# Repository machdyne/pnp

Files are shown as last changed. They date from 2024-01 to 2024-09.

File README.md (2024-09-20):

# Machdyne PNP

## Overview

Machdyne PNP is an open-source project to describe and document the pick-and-place machines that we're using to assist with the assembly of some of our [products](https://machdyne.com).

Instead of a turnkey solution this project will aim to provide examples for anyone who wants (1) to build a custom pick-and-place machine in order to meet their own specific requirements, (2) to understand the machine from the top to bottom, and (3) to have the ability to maintain, modify and repair it.

These machines are designed to work with the [OpenPnP](https://github.com/openpnp/openpnp) software. Instead of attempting to recreate the OpenPnP documentation we will provide links and notes to help you move through the setup process. Our documentation will aim to fill the gaps that we encountered while researching how to build and use such a machine.

### [Machine Eins](machines/eins)

The machine consists of an extruded aluminum frame, linear guide rails, stepper motors, a vacuum pump, a solenoid valve, a controller board, two cameras and a number of 3D-printed parts. The non-printed parts are commonly available. The 3D parts are designed using OpenSCAD. Each part can be printed in about 3 hours or less which allows them to be quickly modified and replaced.

The machine is large (> 1m x 0.6m) but the design is scalable and can be used with a smaller (or larger) frame. The machine is relatively light-weight and must be securely mounted to a sturdy table. It requires a hole in the table for the up-facing camera.

The overall design was inspired by existing open-source pick-and-place machines, primarily the [IndexPnP](https://www.youtube.com/watch?v=YynPThPrJ0o) (the precursor to the [LumenPnP](https://github.com/opulo-inc/lumenpnp)) and [LitePlacer](https://github.com/openpnp/openpnp/wiki/LitePlacer), however all 3D parts have been designed from scratch.

### Machine Zwei

This is a future design based on our experience building and using Eins. Zwei will be more of an assembly assistant than a complete PnP machine. It will be more compact, somewhat portable and it won't require a dedicated table. It is intended for the production of boards with a small number of unique parts, or for placing the most common parts on a larger board (such as decoupling capacitors), or for precisely placing large components.

### [Machdyne AF](https://github.com/machdyne/af)

The [Machdyne AF](https://github.com/machdyne/af) project is a work-in-progress autofeeder system for our PNP machines.

## Funding

This project is being partially funded through the NGI0 Entrust Fund, a fund established by NLnet with financial support from the European Commission's Next Generation Internet programme.

## License

This project is released under the [CERN-OHL-P](LICENSE.txt) license.

The firmware configuration files are released under the GPL3 license.

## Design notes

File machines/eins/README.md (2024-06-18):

# Machdyne PNP - Eins

## Overview

Eins is a simple modular open-source pick and place machine. It is a work-in-progress and this repo will be kept up-to-date as improvements are made. Please feel free to open issues with questions or suggestions.

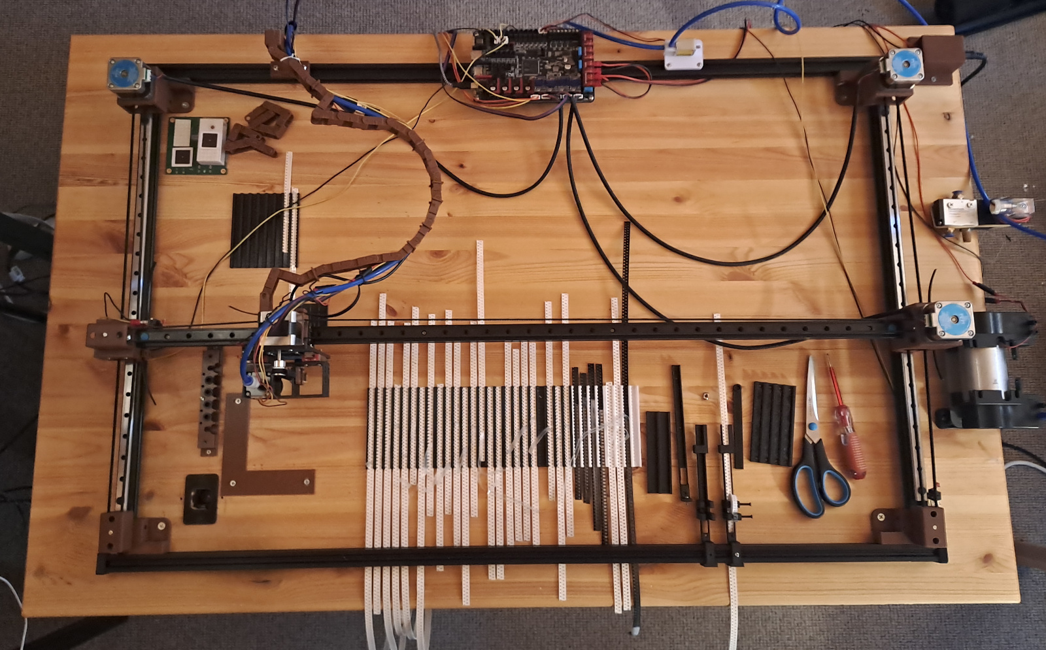
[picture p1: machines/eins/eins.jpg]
eins


This photo is from Jan 2024. You may notice an unused backup solenoid valve on the right side and some passive auto feeder prototypes. The tool changer and multi-strip feeders are not part of this project but can be found below:

  * [Tool changer](https://github.com/richardklingler/openpnp/tree/master/openscad/toolchanger)
  * [Strip feeder](https://www.thingiverse.com/thing:5711658)

The two Y axis motors are connected to a single driver, this is a feature of the controller board.

There is a [video](https://twitter.com/machdyne/status/1705911534369574982) of the machine in action.

## Specifications

| Attribute | Value |
| --- | ----- |
| Table size | 1200mm x 750mm |
| Machine size | ~1000mm x ~650mm |
| Work area | ~850mm x ~450mm |
| Minimum tested part size | 0402 |
| Max placement speed | YTBD |

## Documentation

  * [Assembly Guide](docs/ASSEMBLY.md)

## Parts

The 3D-printable parts are located in the [3d](3d) directory as [OpenSCAD](https://openscad.org) files. You can use OpenSCAD to customize and generate the [STL](3d/stl) files, which can then be sliced and printed.

| Part | Model | Quantity | Description |
| ---- | ----- | --- | --- |
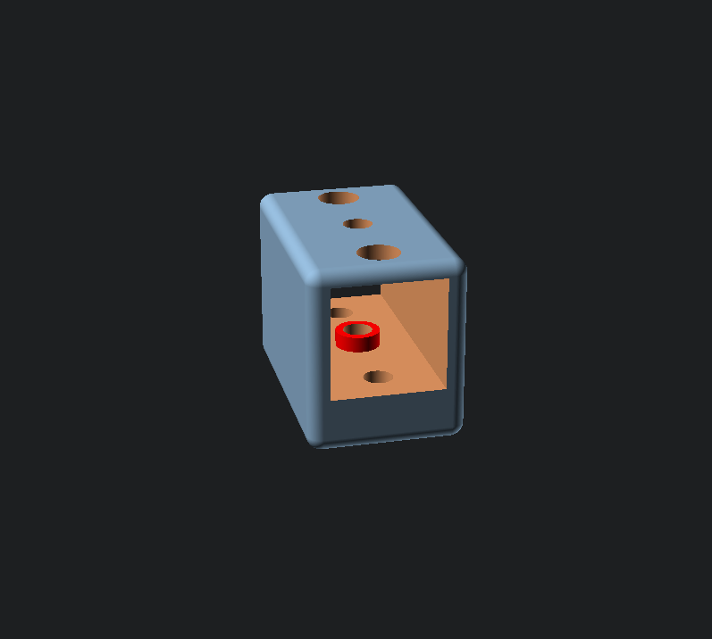
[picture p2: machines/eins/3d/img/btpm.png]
btpm
| [btpm](3d/stl/btpm.stl) |  | 3 | **Belt tension pulley mount.** Holds the belt in place at the opposite end of the axis as the motor, using a pulley and steel dowel. |
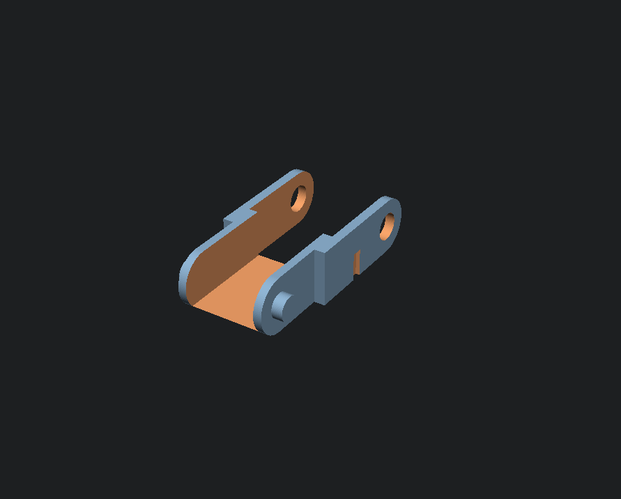
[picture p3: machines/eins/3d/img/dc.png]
dc
| [dc](3d/stl/dc.stl) |  | 1 | **Drag chain links, clips and tower.** Keeps wires, cables and tubing lifted above the work area. The current design sags a bit when the chain is long and needs to be improved. We recommend using a commodity dragchain instead. |
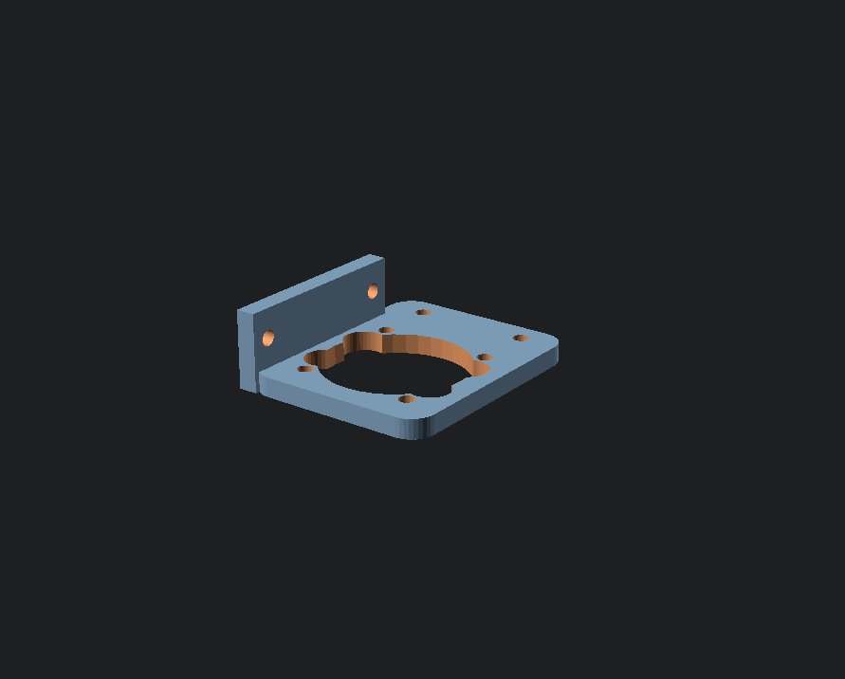
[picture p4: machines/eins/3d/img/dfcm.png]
dfcm
| [dfcm](3d/stl/dfcm.stl) |  | 4 | **Down-facing camera mount.** Holds the down-facing camera. Attaches to the bottom rear side of the Z Gantry Mount Faceplate. |
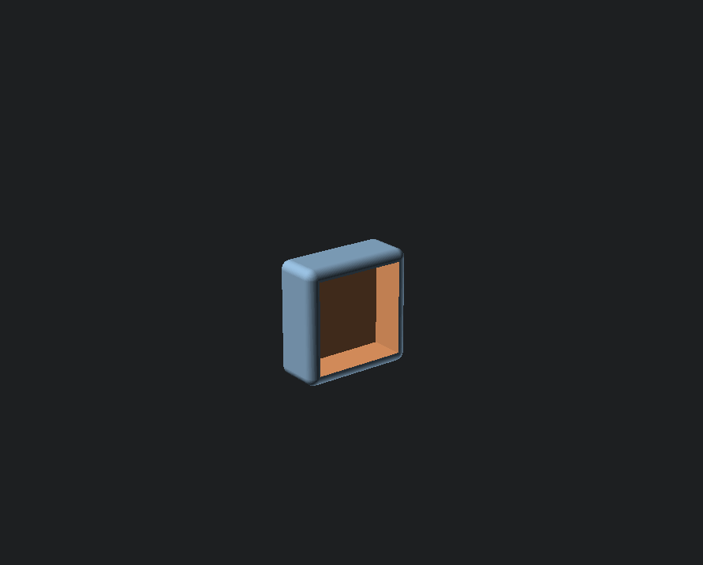
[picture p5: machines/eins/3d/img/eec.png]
eec
| [eec](3d/stl/eec.stl) |  | 1 | **Extrusion end cap.** Covers sharp edges at the ends of the aluminum extrusions. |
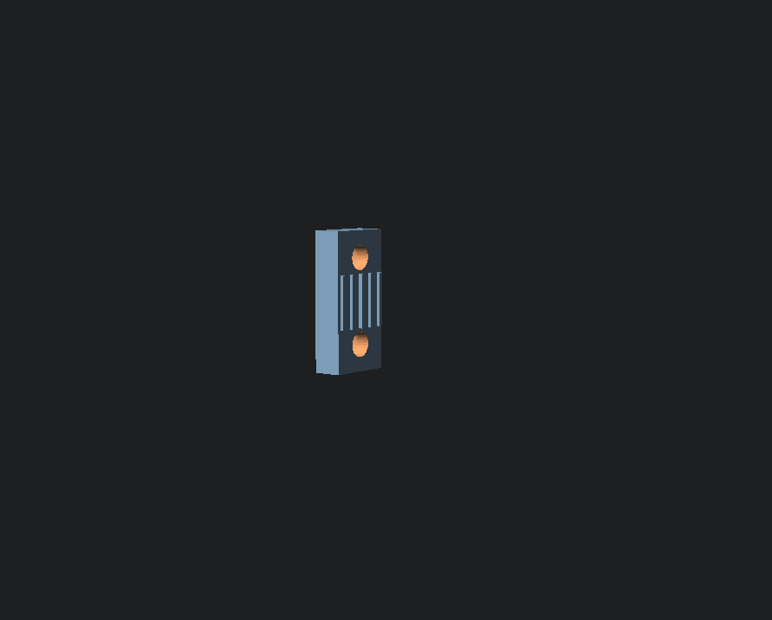
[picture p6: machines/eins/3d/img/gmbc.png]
gmbc
| [gmbc](3d/stl/gmbc.stl) |  | 6 | **Gantry mount belt clamp.** Attaches belt ends to gantry mounts. |
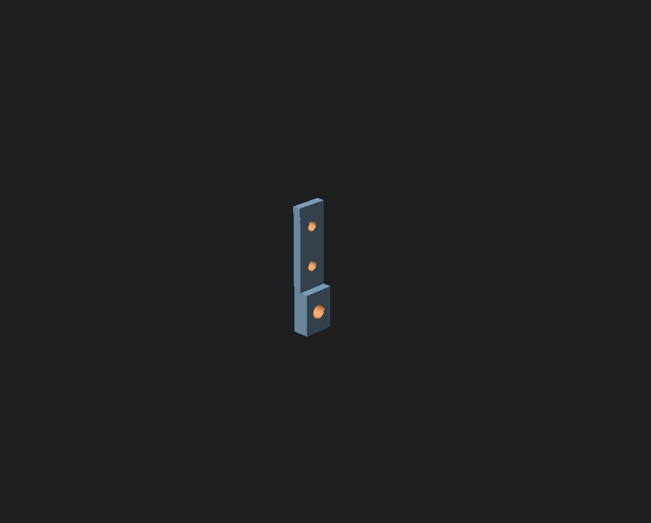
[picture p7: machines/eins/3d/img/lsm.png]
lsm
| [lsm](3d/stl/lsm.stl) |  | 2 | **Limit switch mount.** Attaches X and Y limit switches to the frame. |
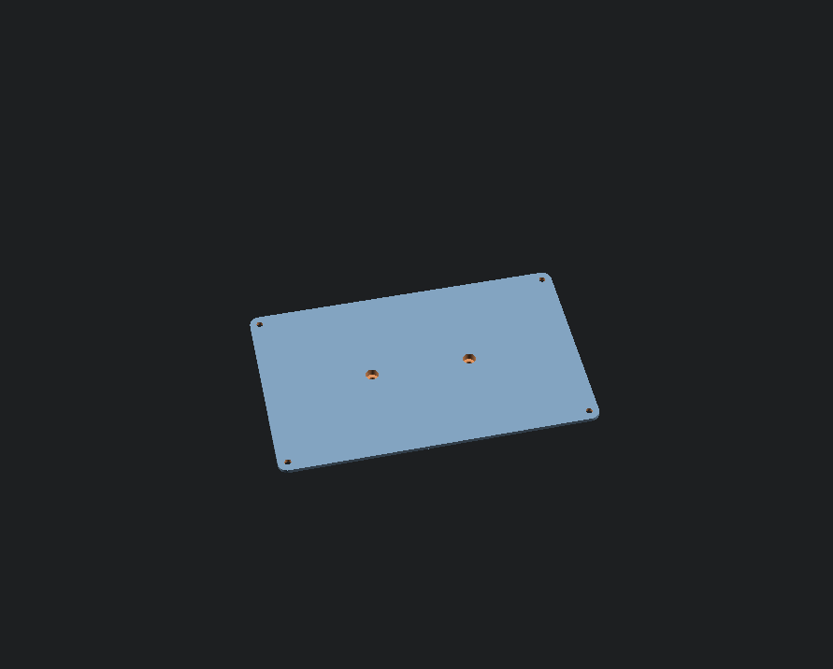
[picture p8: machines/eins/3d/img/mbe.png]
mbe
| [mbe](3d/stl/mbe.stl) |  | 1 | **Mainboard enclosure.** Mounts the controller board to the frame. Not actually enclosed at the moment. |
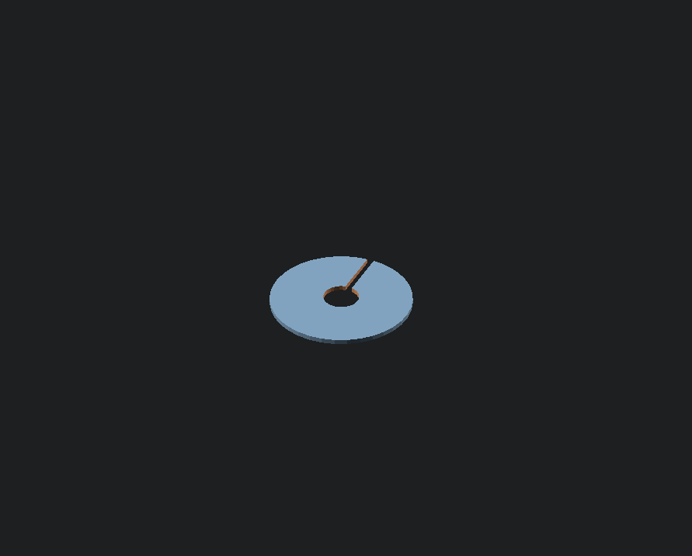
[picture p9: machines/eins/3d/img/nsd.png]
nsd
| [nsd](3d/stl/nsd.stl) |  | 1 | **Nozzle shade disc.** Reduces reflections from the up-facing camera lights on motor. |
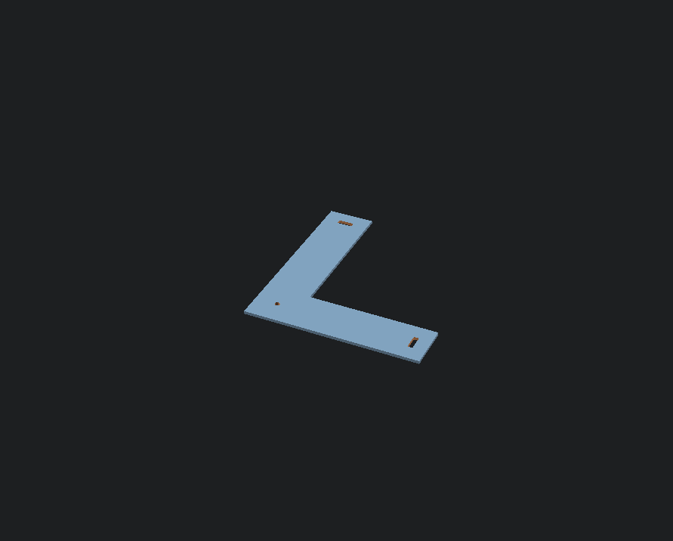
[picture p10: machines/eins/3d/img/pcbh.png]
pcbh
| [pcbh](3d/stl/pcbh.stl) |  | 1 | **PCB holder.** Holds the PCB during assembly. Top screw also acts as homing position. |
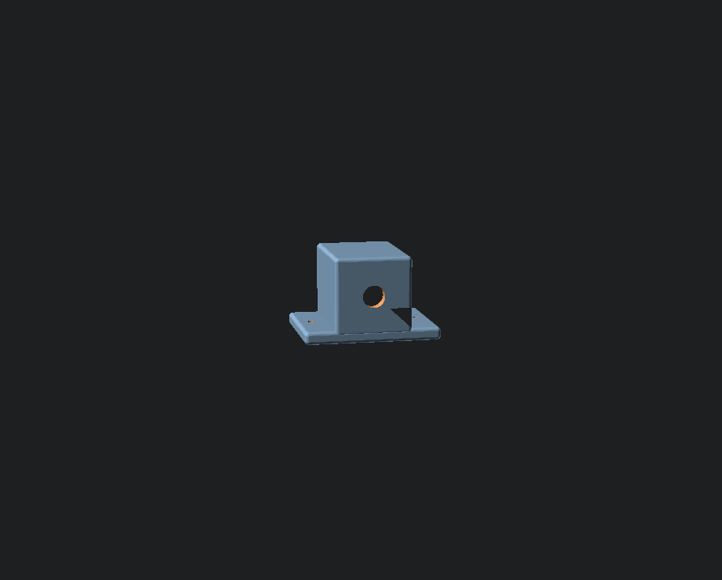
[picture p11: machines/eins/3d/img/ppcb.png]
ppcb
| [ppcb](3d/stl/ppcb.stl) |  | 1 | **Power plug connection box.** Adapts the power supply plug to the controller board. |
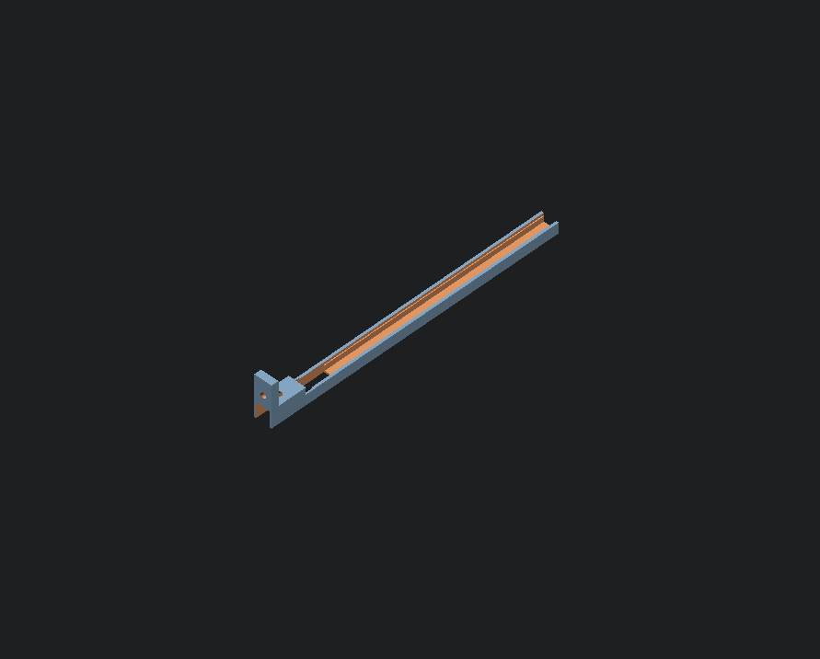
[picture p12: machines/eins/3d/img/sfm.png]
| [sfm](3d/stl/sfm.stl) |  | 1 | **Strip feeder manual.** Manual single feeder for 8mm tapes. |
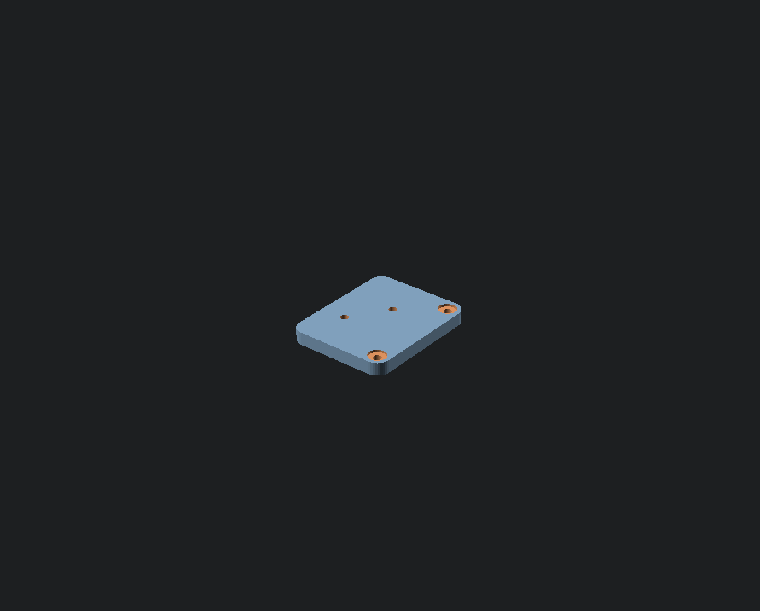
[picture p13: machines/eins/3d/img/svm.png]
| [svm](3d/stl/svm.stl) |  | 1 | **Solenoid valve mount.** Mounts the solenoid valve to the frame. |
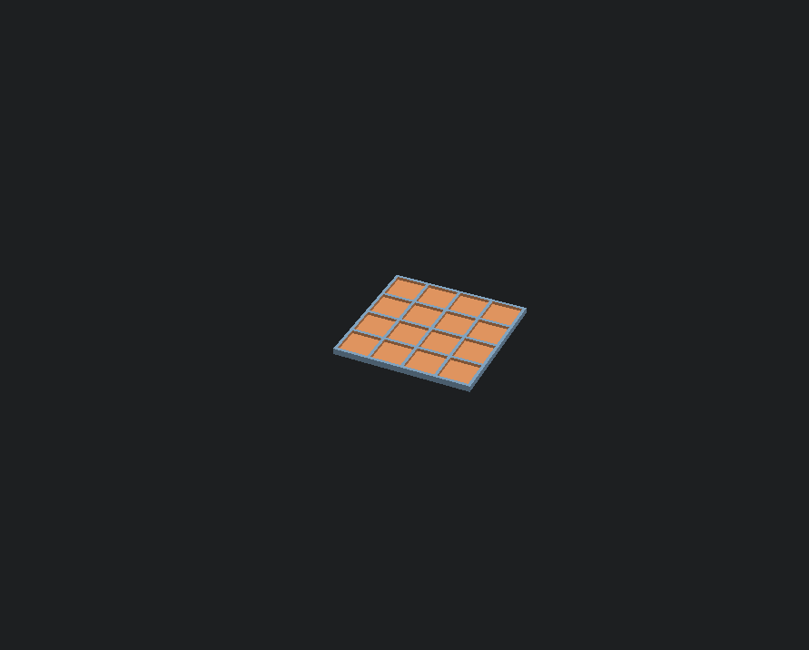
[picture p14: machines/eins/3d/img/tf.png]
tf
| [tf](3d/stl/tf.stl) |  | 1 | **Tray feeder.** Generic customizable tray feeder for ICs. Can be attached to the table with tape. |
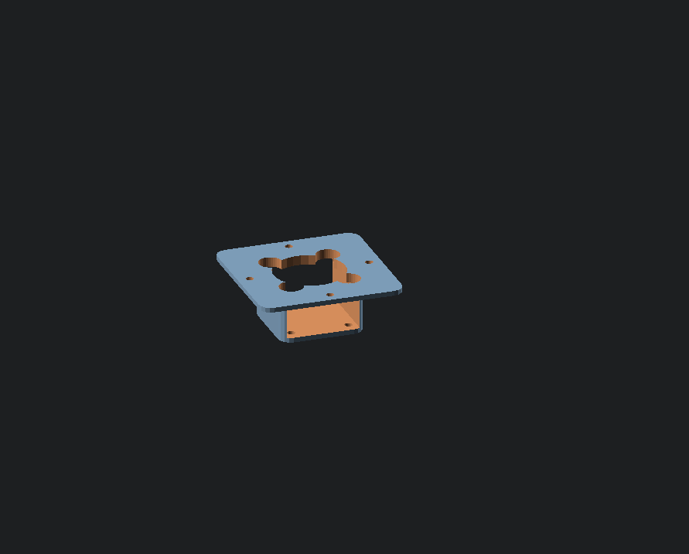
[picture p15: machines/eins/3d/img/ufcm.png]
ufcm
| [ufcm](3d/stl/ufcm.stl) |  | 1 | **Up-facing camera mount.** Mounts the bottom camera underneath the table. |
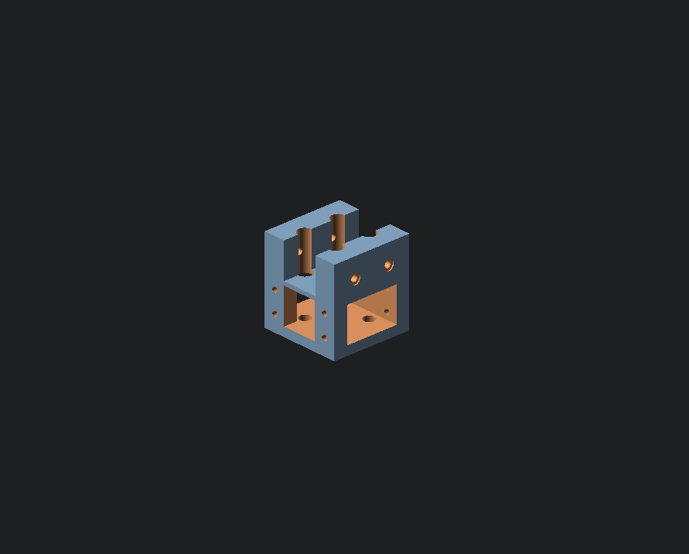
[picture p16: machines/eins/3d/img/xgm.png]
xgm
| [xgm](3d/stl/xgm.stl) |  | 2 | **X gantry mount.** Mounts the X gantry to the Y axis rail. |
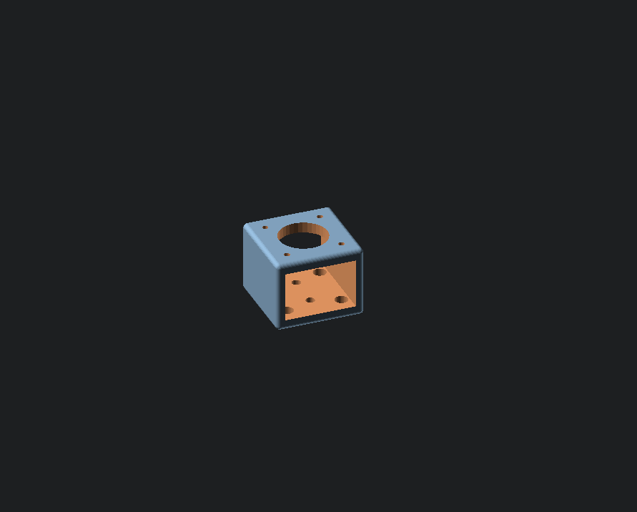
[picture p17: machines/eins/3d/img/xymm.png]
xymm
| [xymm](3d/stl/xymm.stl) |  | 3 | **X+Y motor mount.** Mounts the X and Y motors to their axes. |
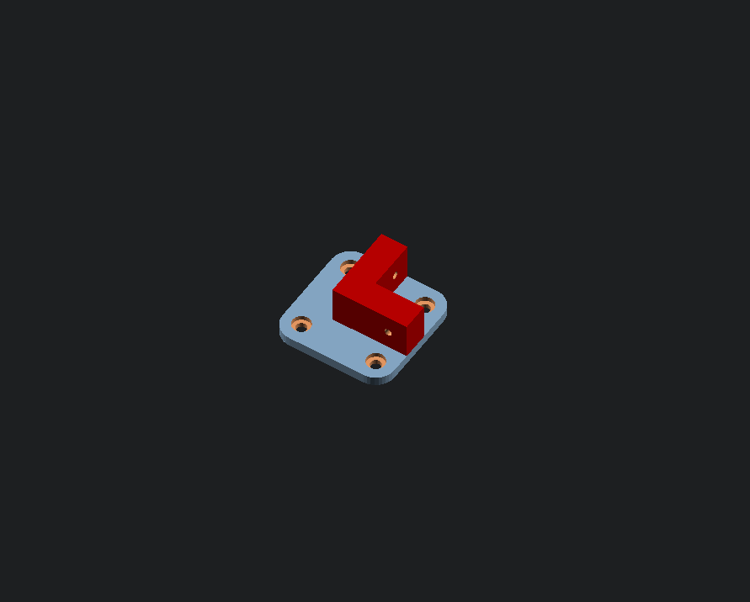
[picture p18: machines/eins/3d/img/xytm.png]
xytm
| [xytm](3d/stl/xytm.stl) |  | 4 | **X+Y table mount.** Mounts the machine to the table. |
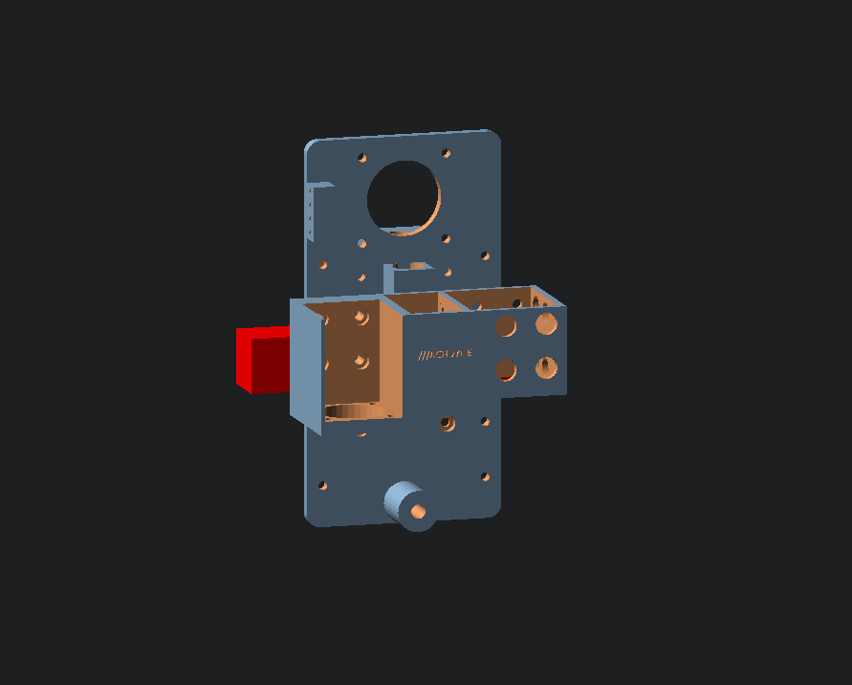
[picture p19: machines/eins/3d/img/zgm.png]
zgm
| [zgm](3d/stl/zgm.stl) |  | 1 | **Z gantry mount, faceplate and assembly mount.** The Z gantry mount ([zgm](3d/stl/zgm.stl)) connects to the belt ends and sits on the X axis. Attached to the zgm is the Z gantry mount faceplate ([zgmfp](3d/stl/zgmfp.stl)) where the Z axis rails are mounted, and to those rails, the Z assembly mount ([zam](3d/stl/zam.stl)), which moves along the Z axis. The Z limit switch attaches to the upper left of the faceplate. |

## Bill of Materials

| Part | Quantity | Description | Example P/N |
| ---- | --- |--- | --- |
| Controller board | 1 | BIGTREETECH Octopus V1.1 Controller board + 4x TMC2209 drivers | KINPRINT-UUU001949 |
| (a) Stepper motors | 4 | 42x42x38mm, 1.68A, 1.8deg, 1.65ohm | 800-001-0782 |
| or (b) Stepper motors | 4 | 42x42x38mm, 1.5A, 0.9deg, 2ohm | 17ME15-1504S |
| Hollow stepper motor set | 1 | 28mm NEMA 11 hollow shaft, D6 rotary joint, CP40 holder | |
| Nozzles | 1+ | CP40 nozzles, N045, N14, N24 | |
| Power supply | 1 | Enclosed desktop supply, 24V 5A 120W, 2.5mm plug | GST120A24-P1M |
| Power jack | 1 | 2.5mm power socket | DC-099 |
| Cameras | 2 | 1MP USB modules | HBV-W202012HD |
| LEDs | 12 | White LEDs 5mm | |
| Vacuum pump | 1 | 24V 10-15L/min 6mm ID | B0BVZR96HN |
| Solenoid valve | 1 | 24V N/O 4mm ID | | 
| Pneumatic tubing | 1 | 6mm ID + 4mm ID + adapters + couplers | | 
| Limit switches | 3 | Roller lever 3 pin limit switches | B07F9QKTQQ |
| Frame X axes | 3 | Aluminum extrusion, 2020V, 1000mm | AW051-2020V-1000 |
| Frame Y axes | 2 | Aluminum extrusion, 2020V, 600mm | AW051-2020V-600 |
| Rail X axis | 1 | Linear rail, MGN12H, 900mm | MGN12H1R900-1 |
| Rail Y axes | 2 | Linear rails, MGN12H, 500mm | 4801151PQ8 |
| Rail Z axes | 2 | Linear rails, MGN9H, 100mm | B08GWVV75C |
| Steel dowels | 3 | 5mm diameter x 25mm long | B07NXPQ717 |
| GT2 belt kits | 2 | Belts and pulleys, 6mm wide, 2mm pitch | B07RBK4GRL |
| Drag chain | 1 | 10x20 drag chain; 1m | 734900622184 |

Note: Use the (a) stepper motors if more concerned with speed; or the (b) stepper motors if more concerned with accuracy.

You will need an assortment of lengths of M3 and M5 bolts, nuts and T-nuts and screws. You will also need some M2 bolts and nuts to attach the limit switches.

## Tools

In addition to a 3D printer you will likely need a variety of tools, including screwdrivers, wire strippers, crimpers, a soldering iron, a drill, etc.

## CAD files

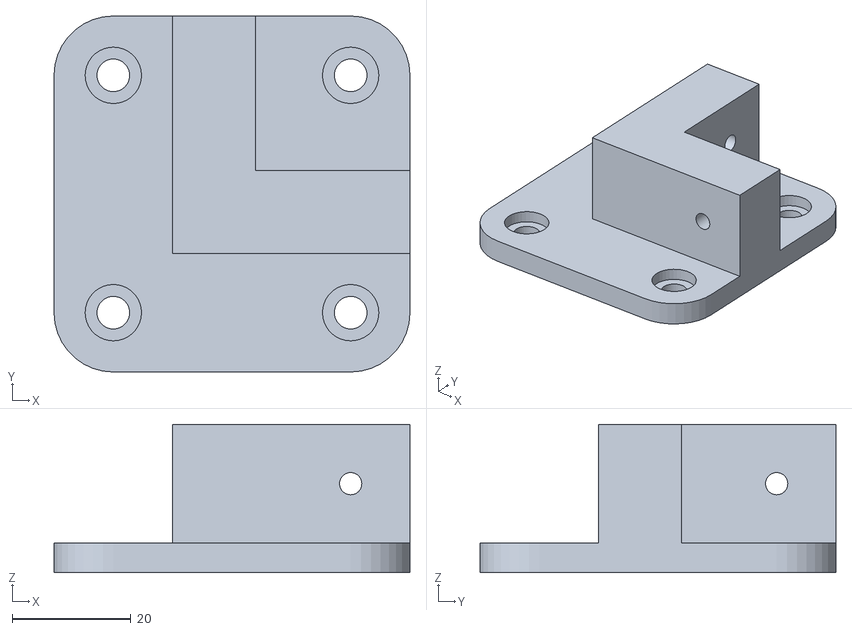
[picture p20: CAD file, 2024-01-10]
machines/eins/3d/stl/xytm.stl
60.0 x 60.0 x 25.0

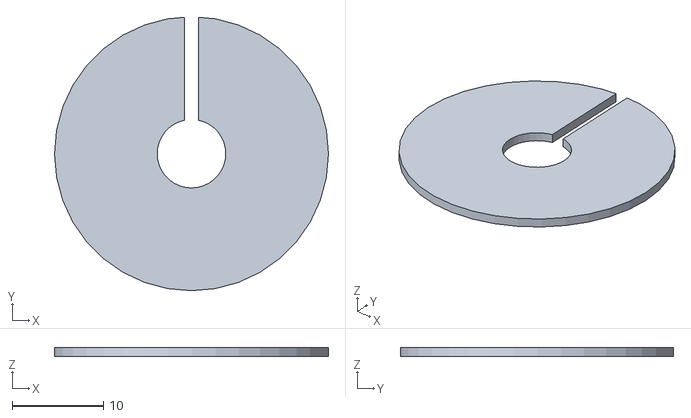
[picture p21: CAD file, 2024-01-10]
machines/eins/3d/stl/nsd.stl
30.0 x 29.9 x 1.00

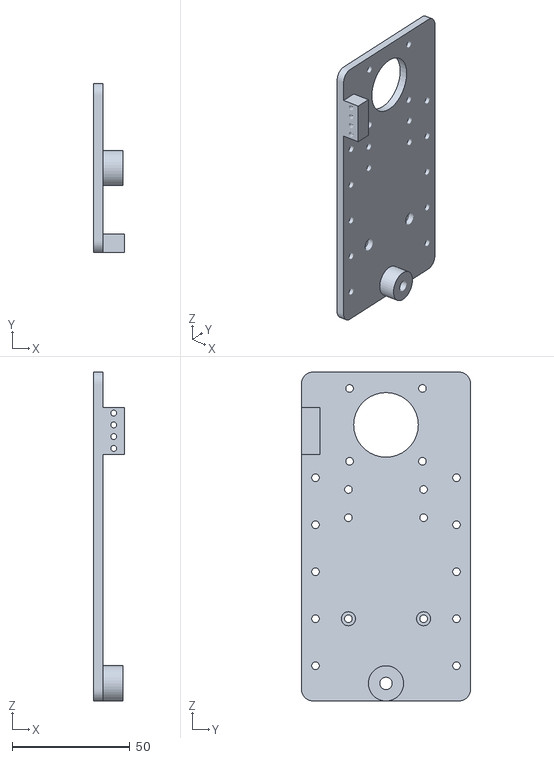
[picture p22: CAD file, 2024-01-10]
machines/eins/3d/stl/zgmfp.stl
13.0 x 72.0 x 140.0

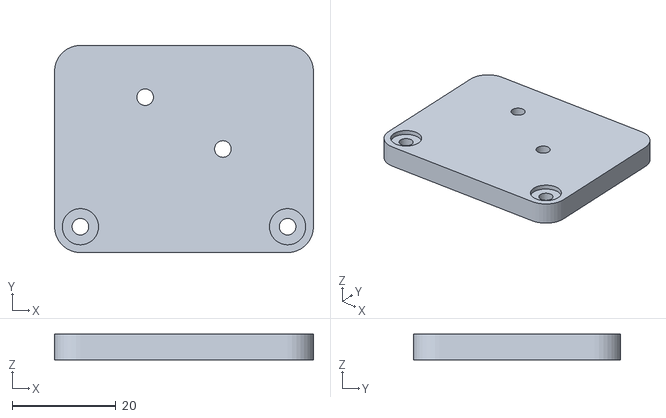
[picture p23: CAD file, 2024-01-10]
machines/eins/3d/stl/svm.stl
50.0 x 40.0 x 5.00

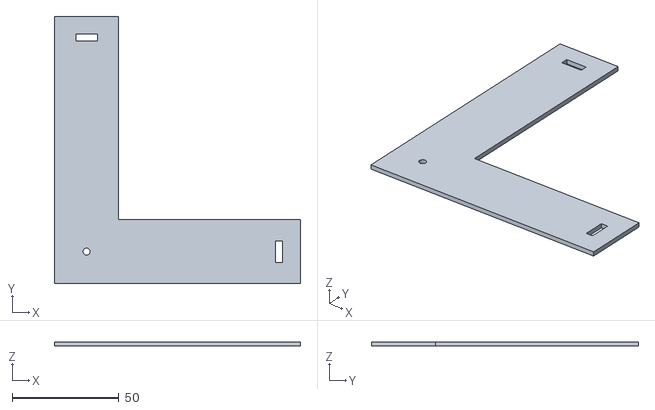
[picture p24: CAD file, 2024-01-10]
machines/eins/3d/stl/pcbh.stl
115.0 x 125.0 x 2.00

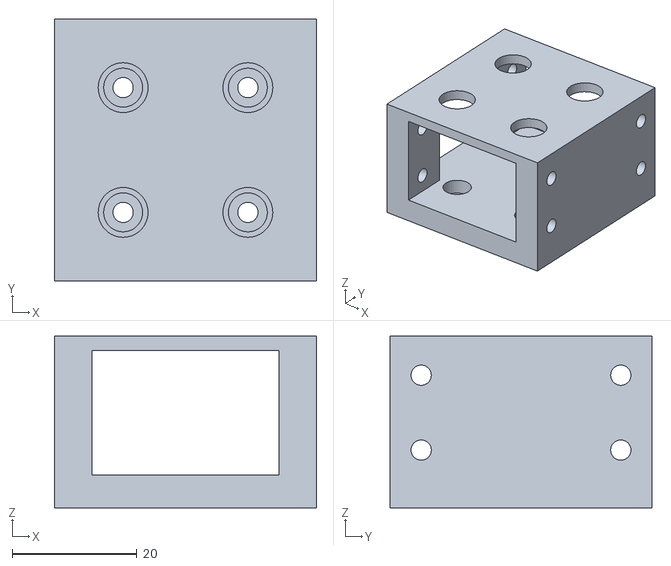
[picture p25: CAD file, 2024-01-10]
machines/eins/3d/stl/zgm.stl
42.0 x 42.0 x 27.5

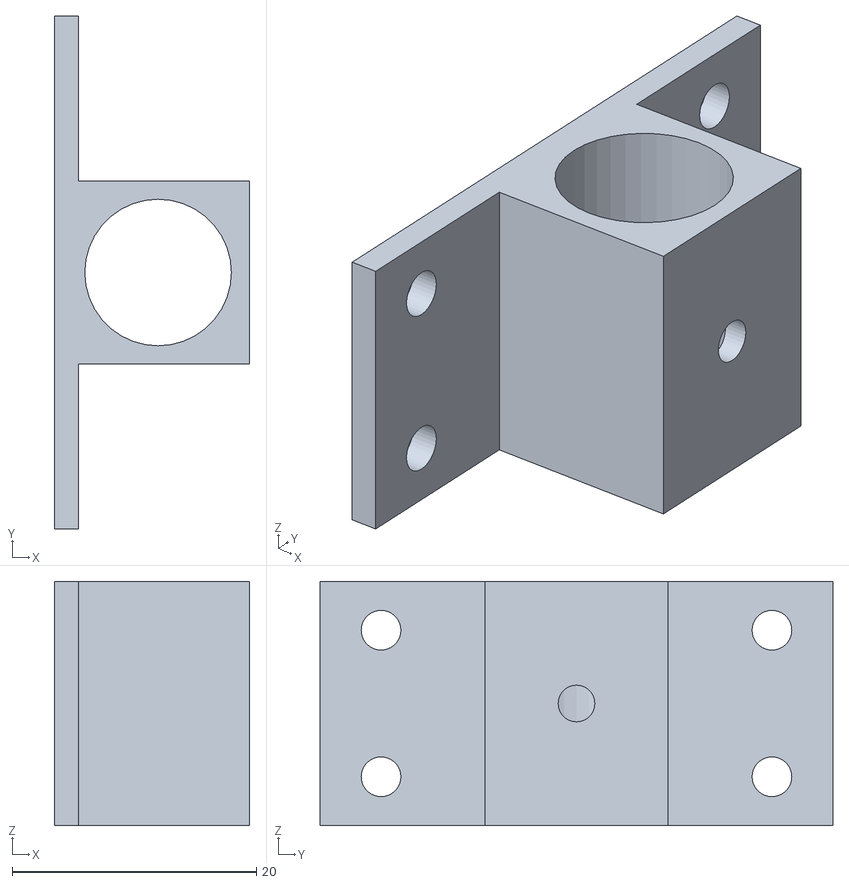
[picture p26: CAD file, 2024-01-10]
machines/eins/3d/stl/zgmfpp.stl
16.0 x 42.0 x 20.0

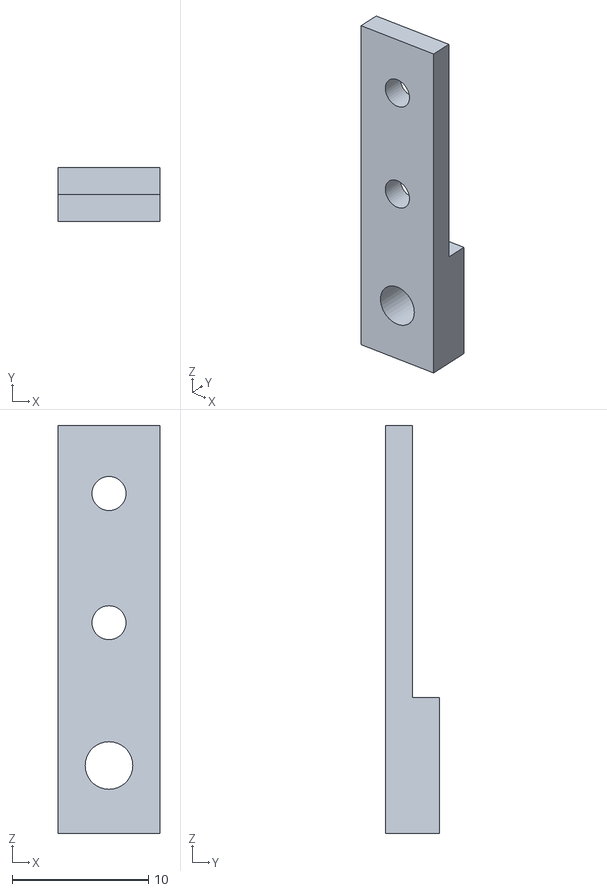
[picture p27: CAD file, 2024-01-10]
machines/eins/3d/stl/lsm.stl
7.50 x 4.00 x 30.0

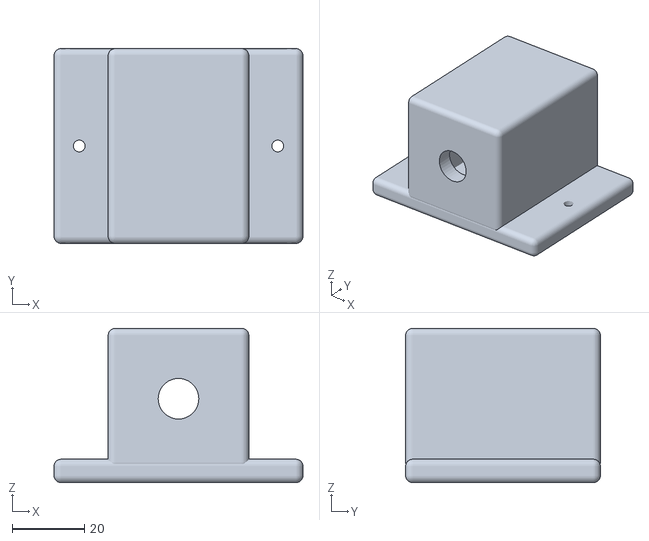
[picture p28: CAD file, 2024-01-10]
machines/eins/3d/stl/ppcb.stl
69.0 x 54.0 x 42.7

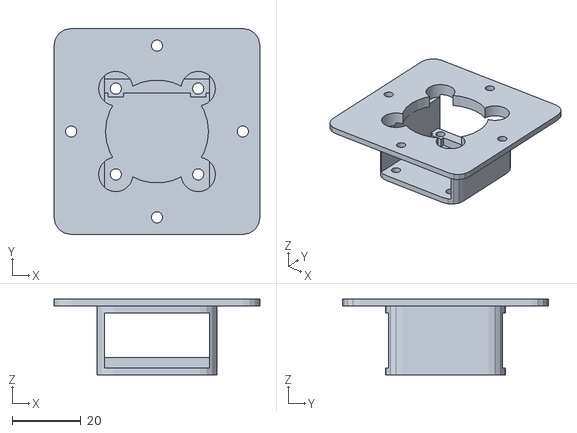
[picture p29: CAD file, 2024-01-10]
machines/eins/3d/stl/ufcm.stl
60.0 x 60.0 x 22.0

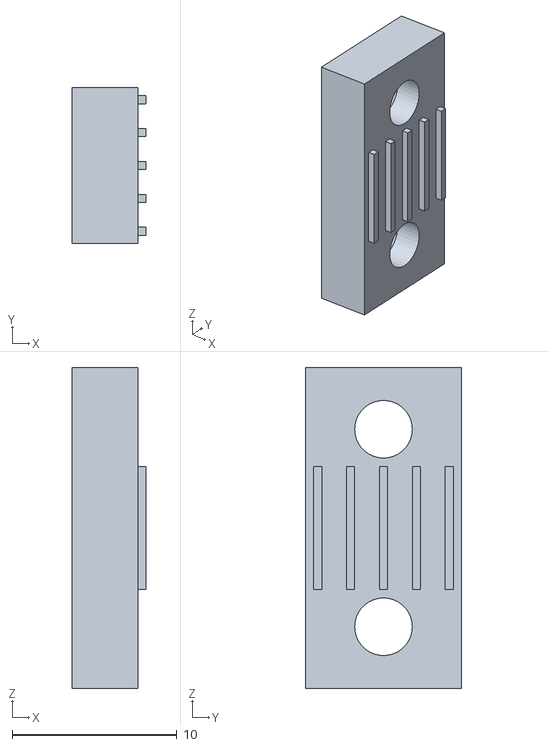
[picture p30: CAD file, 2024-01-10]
machines/eins/3d/stl/gmbc.stl
4.50 x 9.50 x 19.5

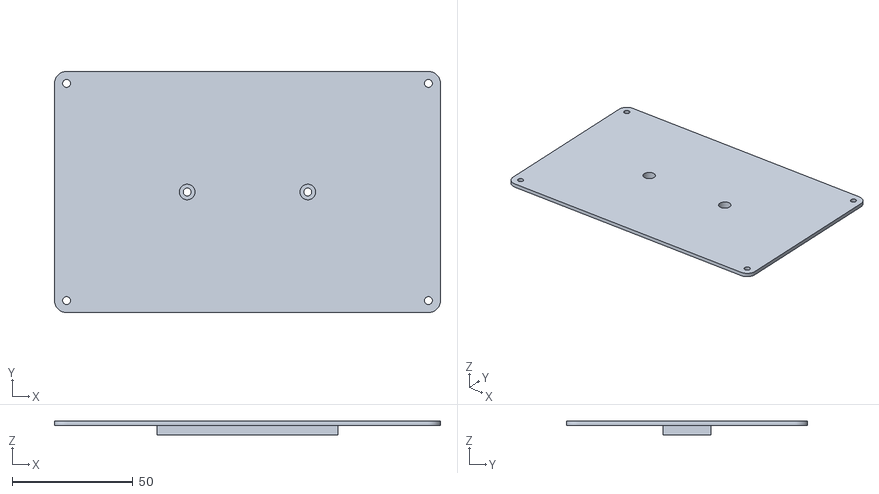
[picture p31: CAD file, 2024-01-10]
machines/eins/3d/stl/mbe.stl
160.0 x 100.0 x 6.00

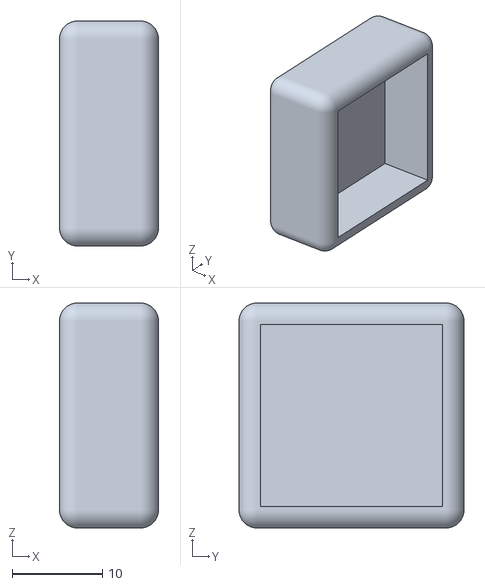
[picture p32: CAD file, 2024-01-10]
machines/eins/3d/stl/eec.stl
11.0 x 25.0 x 25.0

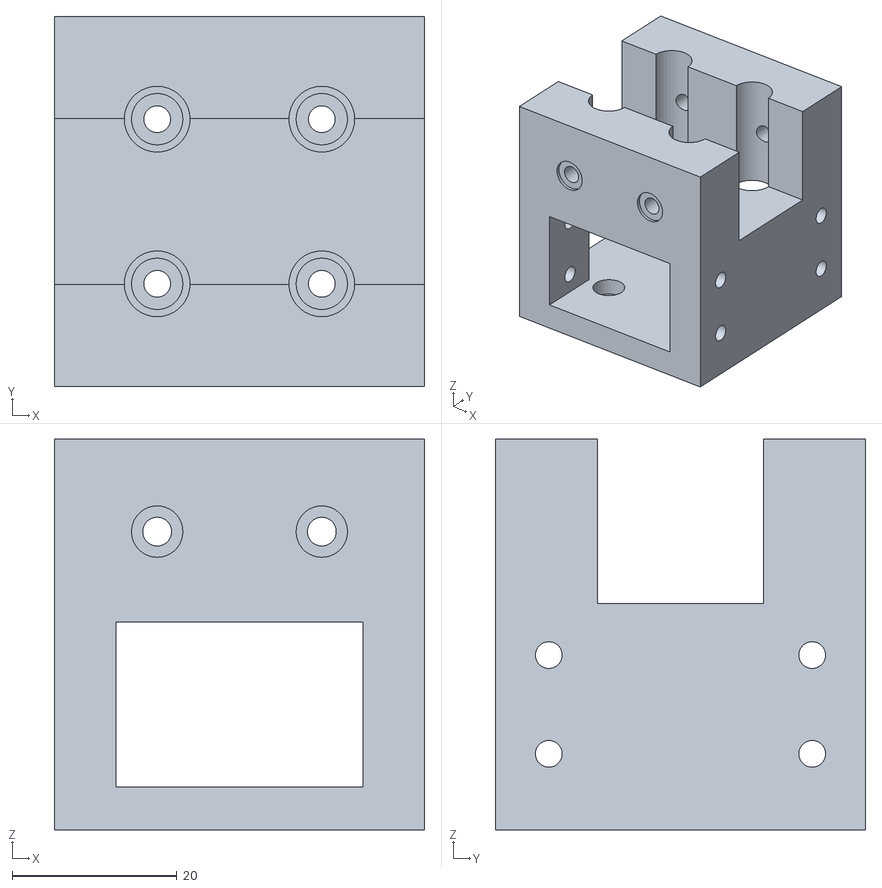
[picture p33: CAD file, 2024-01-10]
machines/eins/3d/stl/xgm.stl
45.0 x 45.0 x 47.5

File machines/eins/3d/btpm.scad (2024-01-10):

/*
 * Machdyne PNP
 * Copyright (c) 2023 Lone Dynamics Corporation. All rights reserved.
 *
 * Belt Tension Pulley Mount
 *
 */
 
$fn = 360;
 
btpm();

module btpm() {
	
//	color([1.0,0,0]) translate([0,-30,-4]) cube([10,10,10]);
	
	difference() {
		color([1.0,0,0]) translate([0,0,-1.25]) cylinder(d=8, h=10);
		translate([0,0,16.75]) cylinder(d=5.25, h=50, center=true);
	}
	
	difference() {

		minkowski() {
			translate([0,0,12.5]) cube([27.5-5,45-5,32.5-5], center=true);
			sphere(2.5);
		}
		
		translate([0,0,16]) cube([20,50,20], center=true);	
		translate([0,0,16.75]) cylinder(d=5.25, h=50, center=true);
		
		// tool hole
		translate([0,15,60]) cylinder(d=7.5, h=100, center=true);
		translate([0,-15,60]) cylinder(d=7.5, h=100, center=true);

		// mounting bolt hole
		translate([0,15,20]) cylinder(d=5.2, h=100, center=true);
		translate([0,-15,20]) cylinder(d=5.2, h=100, center=true);
		
		// countersink hole
//		translate([0,15,48.75+2]) cylinder(d=6.25, h=100, center=true);
//		translate([0,-15,48.75+2]) cylinder(d=6.25, h=100, center=true);
	
	}
	
}

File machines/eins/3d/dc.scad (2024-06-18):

/*
 * Machdyne PNP
 * Copyright (c) 2023 Lone Dynamics Corporation. All rights reserved.
 *
 * Drag Chain Link & Accessories
 *
 */

$fn = 100;

dctc();
//dct();
//dcl();
//color([0,0,1]) dcc();

// drag chain link
module dcl() {
	
	difference() {
		union() {
			cube([20,20,10], center=true);
			translate([10,0,0]) cube([20,16,10], center=true);
			translate([20,0,0]) rotate([90,0,0]) cylinder(d=10, h=16, center=true);
			translate([20,0,0]) rotate([90,0,0]) cylinder(d=4.5, h=20, center=true);
			
			translate([-10,0,0]) rotate([90,0,0]) cylinder(d=10, h=20, center=true);
		}
		
		translate([0,0,2]) cube([50,13,11], center=true);		
		translate([-27.5,0,2]) cube([50,14,20], center=true);		
		translate([-25,0,2]) cube([60,16.5,20], center=true);		
		
		translate([-10,0,0]) rotate([90,0,0]) cylinder(d=5, h=30, center=true);
		
		// clip notches
		translate([0,10,-2.5]) cube([2,1.5,5], center=true);
		translate([0,-10,-2.5]) cube([2,1.5,5], center=true);
		
	}
	

}

// drag chain clip
module dcc() {

	translate([0,0,6]) cube([1.9,21,2], center=true);
	
	translate([0,11.25,0]) cube([1.9,2,14], center=true);
	translate([0,-11.25,0]) cube([1.9,2,14], center=true);
	
	translate([0,-9.25,-6]) cube([1.9,5,2], center=true);
	translate([0,9.25,-6]) cube([1.9,5,2], center=true);
	
	translate([0,9.8,-2.55]) cube([1.9,0.9,4.9], center=true);
	translate([0,-9.8,-2.55]) cube([1.9,0.9,4.9], center=true);
	
}

// drag chain tower
module dct() {
	
	difference() {
		
		union() {
			minkowski() {
				cube([20-5,20-5,90], center=true);
				sphere(2.5);
			}
			translate([0,0,-49]) cube([20,50,8], center=true);
	
			translate([-2.5,0,39.5]) {
				rotate([90,0,0]) {
					translate([10,0,0]) cube([20,16,10], center=true);
					translate([20,0,0]) rotate([90,0,0]) cylinder(d=10, h=16, center=true);
					translate([20,0,0]) rotate([90,0,0]) cylinder(d=4.5, h=21, center=true);
				}
			}
		}

		rotate([0,0,90]) {
			translate([-17.5,0,0]) cylinder(d=5.5, h=200, center=true);
			translate([17.5,0,0]) cylinder(d=5.5, h=200, center=true);
		}
		
	}
		
}

// drag chain tower for common drag chain
module dctc() {
	
	difference() {
		
		union() {
			minkowski() {
				cube([15-5,25-5,95], center=true);
				sphere(2.5);
			}
			translate([0,0,-35]) minkowski() {
				cube([20-5,25-5,20], center=true);
				sphere(2.5);
			}

			translate([0,0,-49]) cube([20,50,8], center=true);	
		}

		rotate([0,90,0]) translate([-40,5,-25]) cylinder(d=4, h=50);
		rotate([0,90,0]) translate([-40,-5,-25]) cylinder(d=4, h=50);
		
		
		rotate([0,0,90]) {
			translate([-18.5,0,0]) cylinder(d=5.5, h=200, center=true);
			translate([18.5,0,0]) cylinder(d=5.5, h=200, center=true);
		}
		
	}
		
}
module roundedcube(xx, yy, height, radius)
{
    translate([0,0,height/2])
    hull()
    {
        translate([radius,radius,0])
        cylinder(height,radius,radius,true);

        translate([xx-radius,radius,0])
        cylinder(height,radius,radius,true);

        translate([xx-radius,yy-radius,0])
        cylinder(height,radius,radius,true);

        translate([radius,yy-radius,0])
        cylinder(height,radius,radius,true);
    }
}

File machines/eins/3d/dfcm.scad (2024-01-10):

/*
 * Machdyne PNP
 * Copyright (c) 2023 Lone Dynamics Corporation. All rights reserved.
 *
 * Down-Facing Camera Mount (for W202012HD cameras)
 *
 */

$fn = 36;

//dfcmt();
//dfcmc();
dfcm();

// clip
module dfcmc() {
	difference() {
		union() {
			translate([-40/2-8.5, -40/2, 10]) roundedcube(7.5,40,2,2.5);			
			translate([-40/2-4.75-2, -40/2+20, 10]) cube([1,15,1], center=true);
			translate([-40/2-4.75+2, -40/2+20, 10]) cube([1,15,1], center=true);
			translate([-40/2-4.75, -40/2+20, 10]) cube([1,15,1], center=true);
		}
		translate([-25,12,-20]) cylinder(d=3.25, h=50, $fn=36);
		translate([-25,-12,-20]) cylinder(d=3.25, h=50, $fn=36);
	}
}

// tool for installing the camera mount
module dfcmt() {

	difference() {
		union() {
			cube([100,10,3], center=true);
			translate([-50,0,1]) cylinder(d=10, h=5, center=true);
		}
		translate([-50,0,-0.5]) cylinder(d=7, h=5, $fn=6);
	}
}

module dfcm() {

	difference() {

		union() {
			translate([-40/2-10, -40/2, 0]) roundedcube(50,40,4,5);
			translate([0,-20,8]) cube([40,4,16], center=true);
		}
		
		translate([0,-35/2+2,-10]) cube([30.5,70,16], center=true);
		translate([0,0,10]) cylinder(d=30, h=40, center=true);
		
		translate([6,12.5,10]) cylinder(d=8.5, h=40, center=true);
		translate([-6,12.5,10]) cylinder(d=8.5, h=40, center=true);
		translate([6,-12.5,10]) cylinder(d=8.5, h=40, center=true);
		translate([-6,-12.5,10]) cylinder(d=8.5, h=40, center=true);

		rotate([90,90,0]) {
			translate([-10,16,-0]) cylinder(d=3.25, h=100, center=true);
			translate([-10,-16,0]) cylinder(d=3.25, h=100, center=true);
		}
	
		// camera mount holes
		translate([-12.5,-12,-5]) cylinder(d=3.25, h=15, $fn=36);
		translate([12.5,-12,-5]) cylinder(d=3.25, h=15, $fn=36);
		translate([-12.5,12,-5]) cylinder(d=3.25, h=15, $fn=36);
		translate([12.5,12,-5]) cylinder(d=3.25, h=15, $fn=36);	
		
		// cable clamp hole
		translate([-25,12,-5]) cylinder(d=3.25, h=15, $fn=36);
		translate([-25,-12,-5]) cylinder(d=3.25, h=15, $fn=36);
	}

}

module roundedcube(xx, yy, height, radius)
{
    translate([0,0,height/2])
    hull()
    {
        translate([radius,radius,0])
        cylinder(height,radius,radius,true);

        translate([xx-radius,radius,0])
        cylinder(height,radius,radius,true);

        translate([xx-radius,yy-radius,0])
        cylinder(height,radius,radius,true);

        translate([radius,yy-radius,0])
        cylinder(height,radius,radius,true);
    }
}

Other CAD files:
machines/eins/3d/stl/dc.stl
machines/eins/3d/stl/tf.stl
machines/eins/3d/stl/sfm.stl
machines/eins/3d/stl/zam.stl
machines/eins/3d/eec.scad
machines/eins/3d/gmbc.scad
machines/eins/3d/lsm.scad
machines/eins/3d/mbe.scad
machines/eins/3d/nsd.scad
machines/eins/3d/pcbh.scad
machines/eins/3d/ppcb.scad
machines/eins/3d/sfm.scad
machines/eins/3d/stl/dfcm.stl
machines/eins/3d/stl/xymm.stl
machines/eins/3d/svm.scad
machines/eins/3d/tf.scad
machines/eins/3d/ufcm.scad
machines/eins/3d/xgm.scad
machines/eins/3d/xymm.scad
machines/eins/3d/xytm.scad
machines/eins/3d/zgm.scad

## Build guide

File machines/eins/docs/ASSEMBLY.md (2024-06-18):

# Machdyne PNP - Eins - Assembly Guide

## Overview

This guide will walk you through the process of assembling the pick-and-place machine "Eins".

If you have all of the parts pre-printed, it may be possible to build the machine in a day, but the instructions are presented in a way that will also allow you to build the machine incrementally over several days, printing parts as you go, and will allow you to test portions of it before moving forward.

This guide references [3D-printed parts](https://github.com/machdyne/pnp/tree/main/machines/eins#parts) and items from the [Bill of Materials](https://github.com/machdyne/pnp/tree/main/machines/eins#bill-of-materials).

## Step - Prepare the table.

We used an Ikea INGO (120x75) pine table, treated with beeswax. Keep in mind that you will need to cut a hole in the table and drill holes into it. You can use a smaller or larger table, but you may need to adjust the frame and rail sizes.

## Step - Attach the Y axes to the table.

The Y axis is built with the two shorter lengths of aluminum extrusion.

Each Y axis extrusion is attached to the table with two `xytm` (X+Y Table Mount) parts, one at each end.

You can use the longer extrusions to help keep the Y axes aligned in parallel. The longer extrusions will be attached later to form the complete rectangular frame.

We centered the frame on the table, but you could also choose to offset it to one side.

The four `xytm` parts are attached to the table with M5 bolts and nuts. It is sufficient to use only one bolt per `xytm` part. Use a pencil to mark the holes for drilling, once you're satisfied that the frame is square.

The Y axes will be attached to the side of the `xytm` parts with M3 bolts and T-nuts, but you will need to temporarily flip them in the next step so you might want to wait to attach them.

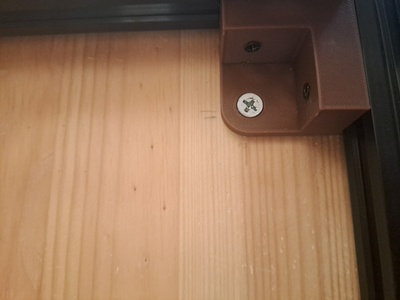
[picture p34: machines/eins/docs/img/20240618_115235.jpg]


## Step - Install the Y axis rails, motor/tension mounts and Y axis motors.

The Y axis linear guide rails allow the rail slide block, and the X gantry that will be attached to it, to travel smoothly along the Y axis.

On each side of the rail an `xymm` (X+Y Motor Mount) and `btpm` (Belt Tension Pulley Mount) part will be attached to the extrusions using M5 bolts and T-nuts. After the `xymm` part is attached, turn it over and attach the motor using M3 bolts.

You can attach the rails to the extrusions using at least three M3 bolts and T-nuts.

Now attach the Y axes to the side of the `xytm` parts using M3 bolts and T-nuts, as shown in the previous step.

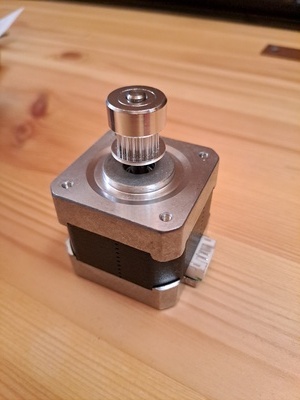
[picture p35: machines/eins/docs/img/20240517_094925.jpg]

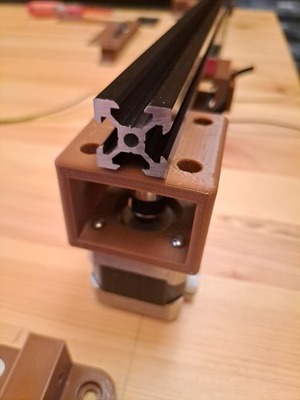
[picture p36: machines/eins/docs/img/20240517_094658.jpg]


## Step - Install the remaining frame extrusions.

In order to complete the rectangular frame, attach the two remaining long extrusions to the near and far side of the `xytm` parts with M3 bolts and T-nuts and attach an `eec` (Extrusion End Cap) to each end.

The long extrusions are used for attaching accessories.

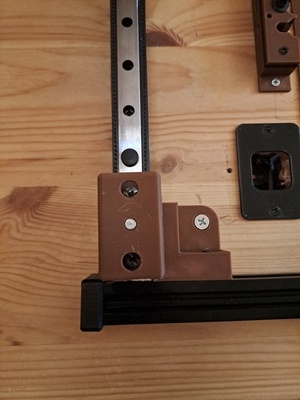
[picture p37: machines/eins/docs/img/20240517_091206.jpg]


## Step - Design your work area.

The most permanent feature of the work area is the up-facing camera hole. The nozzle needs to be able to move freely over the up-facing camera, so it needs to be positioned at least 50mm above the bottom of the Y axis and at least 60mm away from the Y axis.

This is a good time to determine approximately where you want to place the PCB holder, tool changer, feeders, etc.

## Step - Cut the up-facing camera hole.

Cut the up-facing camera hole.

We cut out a ~24 x ~24mm hole by drilling multiple holes and using a chisel, because we didn't have a jigsaw available. You will get a cleaner hole with a proper saw.

## Step - Install the up-facing camera.

Place the `ufcmfp` (Up-facing Camera Mount Faceplate) on the top of the table over the up-facing camera hole and use the `ufcmfp` as a guide for drilling two 3mm holes above and below the camera hole.

Attach the camera to the `ufcm` (Up-facing Camera Mount) with M3 bolts and nuts.

Insert two long M3 bolts into `ufcmfp`, through the table, through the `ufcm` and then fasten nuts on the bottom.

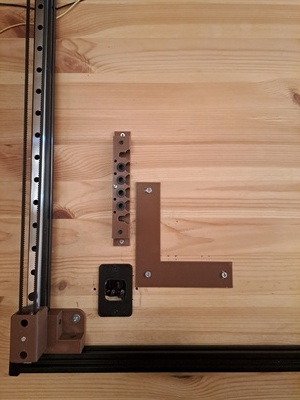
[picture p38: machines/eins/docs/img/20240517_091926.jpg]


## Step - Install the X axis rail, motor/tension mount and X axis motor.

The final `xymm` and `btpm` parts are attached to each side of the final longer extrusion, the X axis extrusion, using M5 bolts and T-nuts.

Attach the X axis rail to the center of the extrusion using several M3 bolts and T-nuts.

After the `xymm` part is attached, turn it over and attach the motor using M3 bolts.

## Step - Install the X gantry.

Attach an `xgm` (X Gantry Mount) on both Y axis rail slide blocks with four M3 bolts each.

The X axis extrusion is attached on each side to an `xgm` with four M3 bolts and T-nuts. This is easier if you attach the bolts and T-nuts first, and then slide the X axis into `xgm` from one side, and then back in the opposite direction into the other `xgm`. When both ends are in place, tighten the bolts.

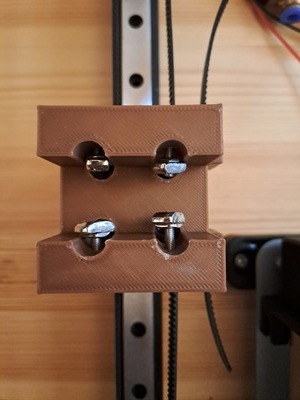
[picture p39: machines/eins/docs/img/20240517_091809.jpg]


## Step - Test Y axis movement.

At this point you should test the Y axis movement and make any adjustments necessary to the rail alignment so that the X gantry can move smoothly along the Y axis.

## Step - Install the Y axis belts.

Attach screwable pulleys to the Y axis motors shafts.

Push the steel dowels partially into each `btpm` center hole, slide a bearing pulley onto the dowel, and push the steel dowel further until it's flush with the top of `btpm`.

The Y axis belts wrap around the motor pulleys on the far side, they pass through `xgm`, then wrap around the `btpm` pulleys on the near side, with the teeth facing inward.

Each end of the belts pass through the `xgm` parts, then out the side, and are fastened with `gmbc` (Gantry Mount Belt Clamp) parts, which are attached using two M3 bolts and nuts each.

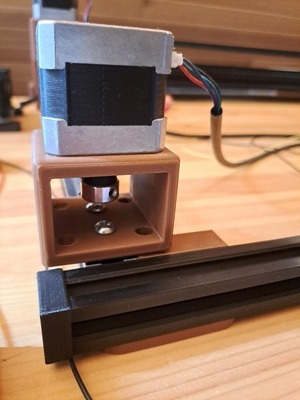
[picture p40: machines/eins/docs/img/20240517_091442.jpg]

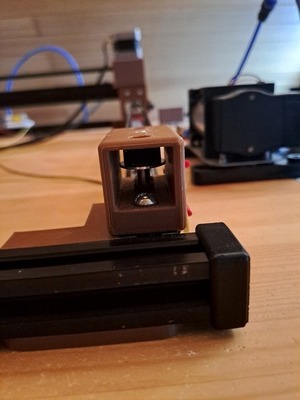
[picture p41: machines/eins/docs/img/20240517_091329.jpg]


## Step - Install the X axis belt.

Attach `zgm` (Z Gantry Mount) to the X axis rail slide block with four M3 bolts, the belt end opening should face the far side of the machine.

The X axis belt wraps around the motor pulley on the right side, it passes through `zgm`, then wraps around the `btpm` pulley on the left side, with the teeth facing inward.

Each end of the belts also pass through the `zgm` part, then out the side, and are fastened with the `gmbc_dcc` (Gantry Mount Belt Clamp - Commodity Dragchain) part, which is attached using M3 bolts and nuts. This part holds the belt ends in place and provides a mount point for the dragchain.

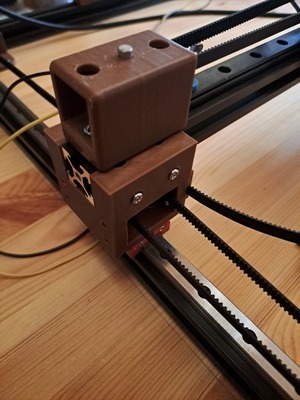
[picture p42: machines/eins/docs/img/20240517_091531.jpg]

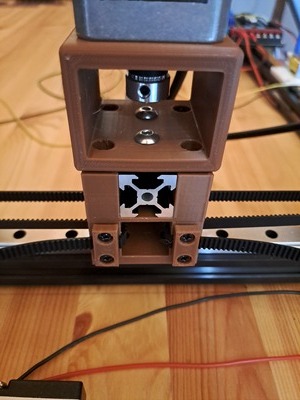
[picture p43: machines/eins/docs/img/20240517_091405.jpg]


## Step - Test the machine.

It's now possible to test the X/Y movement using the motors. You might want to temporarily skip ahead and complete the limit switch and controller installation. There is a `zgmfpp` (Z Gantry Mount Faceplate Plotter) part that will let you attach a pen, and you can use an SVG to g-code converter to draw something on a sheet of paper.

## Step - Install the Z axis.

The `zgmfp` (Z Gantry Mount Faceplate) attaches to `zgm`. Before attaching, the entire Z gantry should be assembled.

This assembly is a smaller version of what you've already done three times.

Mount the two Z axis rails to the front of `zgmfp`.

Next, attach the `zam` (Z Assembly Mount) to the rails with M3 bolts.

Attach the motor to the rear of `zgmfp` with M3 bolts, so that the shaft faces the front. Attach a screwable pulley to the motor shaft.

Slide a bearing pulley onto a long (35-40mm) M5 bolt, and then insert the bolt into the bottom pulley hole. Use nuts on both sides of the spacer to adjust how far the pulley extends, which should be approximately equal to the motor pulley.

The belt wraps around the motor pulley, passes through the center of `zam`, and then wraps around the bottom pulley. The belt ends are passed back through the `zam` and out the side, where two `gmbc` parts hold them in place.

The C axis hollow shaft motor can now be attached to `zam` with M3 bolts.

On the rear side of `zgmfp`, attach the `dfcm` (Down-facing Camera Mount) and camera.

Finally, attach `zgmfp` to `zgm` with four M3 bolts and nuts.

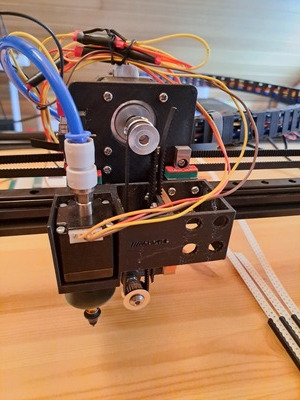
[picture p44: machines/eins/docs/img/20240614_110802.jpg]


## Step - Install the drag chain.

Install the `dctc` (Drag Chain Tower - Commodity) on the far side extrusion using M5 bolts and T-nuts.

Run all wires, cables and tubes through the drag chain.

Attach one of the drag chain ends to the `dct` and the other end to the `gmbc_dcc` that is attached to `zgm`.

## Step - Install the limit switches.

Three limit switches set the zero coordinate for the X, Y and Z axes.

The max coordinates are set in the firmware.

The X/Y limit switches are connected to `lsm` (Limit Switch Mount) with M2 bolts and nuts, which is then connected to the extrusions with M3 bolts and T-nuts.

The X axis limit switch is installed on the Y axis extrusion on the right near side.

The Y axis limit switch is installed the X axis extrusion on the left side.

The Z axis limit switch is attached directly to the `zgmfp`.

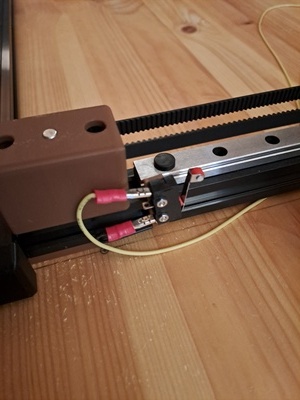
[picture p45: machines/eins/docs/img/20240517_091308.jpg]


## Step - Install the controller.

The controller can be attached to the `mbe` (Mainboard Enclosure) with four M3 bolts and nuts, after it is mounted on the far side of the frame with two M3 bolts and T-nuts.

## Step - Wire the controller.

The `ppcb` (Power Plug Connection Box) can be used to wire a desktop power supply to the controller board, but there are many other possible ways to power the machine.

If using the BIGTREETECH Octopus with the Eins Marlin firmware configuration:

| Connector | Wired to |
|---|---|
| MOTOR0 | X axis |
| MOTOR1 | Z axis |
| MOTOR2 1 | Y axis right |
| MOTOR2 2 | Y axis left |
| MOTOR3 | C axis |
| PG6 | X limit switch |
| PG9 | Y limit switch |
| PG10 | Z limit switch |
| FAN0 | Pump |
| FAN1 | Solenoid |

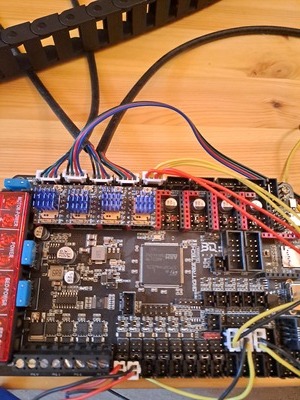
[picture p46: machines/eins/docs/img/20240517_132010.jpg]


## Step - Update the firmware.

Download the Marlin 2.1 source code, install the prerequisites, and replace the configuration files with those in [machines/eins/firmware](machines/eins/firmware).

Build the firmware binary:

```
$ platformio run -e STM32F446ZE_btt_USB
```

Then copy `.pio/build/STM32F446ZE_btt_USB/firmware.bin` to a MicroSD card, plug it into the controller, and turn on the power.

## Step - Test the controller.

You can test basic movements by sending G-code to the controller, but use caution to avoid collisions.

G-code to move the X axis 10mm:

```
G0 X10
```

## Step - Install the pneumatics.

The pump can be mounted to the top, side or bottom of the table.

The `svm` (Solenoid Valve Mount) can be used to mount the solenoid to the far side of the frame.

The pneumatic tubing should be connected from the pump inlet to the solenoid, and the solenoid to the hollow shaft motor that is attached to `zam`.

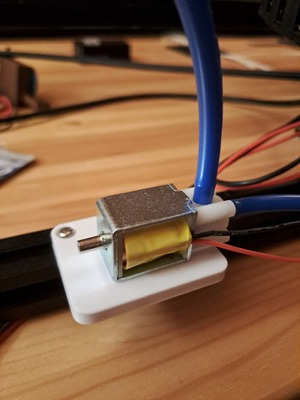
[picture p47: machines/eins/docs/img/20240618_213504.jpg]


## Step - Test the pneumatics.

Move the nozzle over a small piece of paper, move the nozzle down until it's touching the paper, turn on the pump and solenoid, lift the nozzle, and then turn off the solenoid to drop the paper.

G-code to turn the pump on and off:

```
M106 P0 S255
M106 P0 S0
```

G-code to turn the solenoid on and off:

```
M106 P1 S255
M106 P1 S0
```

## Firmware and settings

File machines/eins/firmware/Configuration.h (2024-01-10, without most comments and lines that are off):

#pragma once
#define CONFIGURATION_H_VERSION 02010300
#define STRING_CONFIG_H_AUTHOR "(none, default config)" // Who made the changes.
  #define MOTHERBOARD BOARD_BTT_OCTOPUS_V1_1
#define SERIAL_PORT 1
#define BAUDRATE 115200
#define SERIAL_PORT_2 -1
#define X_DRIVER_TYPE  TMC2209
#define Y_DRIVER_TYPE  TMC2209
#define Z_DRIVER_TYPE  TMC2209
#define I_DRIVER_TYPE  TMC2209
  #define AXIS4_NAME 'A' // :['A', 'B', 'C', 'U', 'V', 'W']
  #define AXIS4_ROTATES
#define EXTRUDERS 0
#define DEFAULT_NOMINAL_FILAMENT_DIA 1.75
#define TEMP_SENSOR_0 1
#define TEMP_SENSOR_1 0
#define TEMP_SENSOR_2 0
#define TEMP_SENSOR_3 0
#define TEMP_SENSOR_4 0
#define TEMP_SENSOR_5 0
#define TEMP_SENSOR_6 0
#define TEMP_SENSOR_7 0
#define TEMP_SENSOR_BED 1
#define TEMP_SENSOR_PROBE 0
#define TEMP_SENSOR_CHAMBER 0
#define TEMP_SENSOR_COOLER 0
#define TEMP_SENSOR_BOARD 0
#define TEMP_SENSOR_SOC 0
#define TEMP_SENSOR_REDUNDANT 0
#define DUMMY_THERMISTOR_998_VALUE  25
#define DUMMY_THERMISTOR_999_VALUE 100
#if TEMP_SENSOR_IS_MAX_TC(0)
  #define MAX31865_SENSOR_OHMS_0      100 // (Ω) Typically 100 or 1000 (PT100 or PT1000)
  #define MAX31865_CALIBRATION_OHMS_0 430 // (Ω) Typically 430 for Adafruit PT100; 4300 for Adafruit PT1000
#endif
#if TEMP_SENSOR_IS_MAX_TC(1)
  #define MAX31865_SENSOR_OHMS_1      100
  #define MAX31865_CALIBRATION_OHMS_1 430
#endif
#if TEMP_SENSOR_IS_MAX_TC(2)
  #define MAX31865_SENSOR_OHMS_2      100
  #define MAX31865_CALIBRATION_OHMS_2 430
#endif
#if HAS_E_TEMP_SENSOR
  #define TEMP_RESIDENCY_TIME         10  // (seconds) Time to wait for hotend to "settle" in M109
  #define TEMP_WINDOW                  1  // (°C) Temperature proximity for the "temperature reached" timer
  #define TEMP_HYSTERESIS              3  // (°C) Temperature proximity considered "close enough" to the target
#endif
#if TEMP_SENSOR_BED
  #define TEMP_BED_RESIDENCY_TIME     10  // (seconds) Time to wait for bed to "settle" in M190
  #define TEMP_BED_WINDOW              1  // (°C) Temperature proximity for the "temperature reached" timer
  #define TEMP_BED_HYSTERESIS          3  // (°C) Temperature proximity considered "close enough" to the target
#endif
#if TEMP_SENSOR_CHAMBER
  #define TEMP_CHAMBER_RESIDENCY_TIME 10  // (seconds) Time to wait for chamber to "settle" in M191
  #define TEMP_CHAMBER_WINDOW          1  // (°C) Temperature proximity for the "temperature reached" timer
  #define TEMP_CHAMBER_HYSTERESIS      3  // (°C) Temperature proximity considered "close enough" to the target
#endif
#if TEMP_SENSOR_REDUNDANT
  #define TEMP_SENSOR_REDUNDANT_SOURCE    E1  // The sensor that will provide the redundant reading.
  #define TEMP_SENSOR_REDUNDANT_TARGET    E0  // The sensor that we are providing a redundant reading for.
  #define TEMP_SENSOR_REDUNDANT_MAX_DIFF  10  // (°C) Temperature difference that will trigger a print abort.
#endif
#define HEATER_0_MINTEMP   5
#define HEATER_1_MINTEMP   5
#define HEATER_2_MINTEMP   5
#define HEATER_3_MINTEMP   5
#define HEATER_4_MINTEMP   5
#define HEATER_5_MINTEMP   5
#define HEATER_6_MINTEMP   5
#define HEATER_7_MINTEMP   5
#define BED_MINTEMP        5
#define CHAMBER_MINTEMP    5
#define HEATER_0_MAXTEMP 275
#define HEATER_1_MAXTEMP 275
#define HEATER_2_MAXTEMP 275
#define HEATER_3_MAXTEMP 275
#define HEATER_4_MAXTEMP 275
#define HEATER_5_MAXTEMP 275
#define HEATER_6_MAXTEMP 275
#define HEATER_7_MAXTEMP 275
#define BED_MAXTEMP      150
#define CHAMBER_MAXTEMP  60
#define HOTEND_OVERSHOOT 15   // (°C) Forbid temperatures over MAXTEMP - OVERSHOOT
#define BED_OVERSHOOT    10   // (°C) Forbid temperatures over MAXTEMP - OVERSHOOT
#define COOLER_OVERSHOOT  2   // (°C) Forbid temperatures closer than OVERSHOOT
#define PIDTEMP           // See the PID Tuning Guide at https://reprap.org/wiki/PID_Tuning
#define PID_MAX  255      // Limit hotend current while PID is active (see PID_FUNCTIONAL_RANGE below); 255=full current
#define PID_K1 0.95       // Smoothing factor within any PID loop
    #define DEFAULT_Kp  22.20
    #define DEFAULT_Ki   1.08
    #define DEFAULT_Kd 114.00
#define MAX_BED_POWER 255 // limits duty cycle to bed; 255=full current
#define MAX_CHAMBER_POWER 255 // limits duty cycle to chamber heater; 255=full current
  #define PID_FUNCTIONAL_RANGE 10 // If the temperature difference between the target temperature and the actual temperature
#define PREVENT_COLD_EXTRUSION
#define EXTRUDE_MINTEMP 170
#define PREVENT_LENGTHY_EXTRUDE
#define EXTRUDE_MAXLENGTH 200
#define THERMAL_PROTECTION_HOTENDS // Enable thermal protection for all extruders
#define THERMAL_PROTECTION_BED     // Enable thermal protection for the heated bed
#define THERMAL_PROTECTION_CHAMBER // Enable thermal protection for the heated chamber
#define THERMAL_PROTECTION_COOLER  // Enable thermal protection for the laser cooling
#define ENDSTOPPULLUPS
#define X_MIN_ENDSTOP_HIT_STATE HIGH
#define X_MAX_ENDSTOP_HIT_STATE HIGH
#define Y_MIN_ENDSTOP_HIT_STATE HIGH
#define Y_MAX_ENDSTOP_HIT_STATE HIGH
#define Z_MIN_ENDSTOP_HIT_STATE HIGH
#define Z_MAX_ENDSTOP_HIT_STATE HIGH
#define I_MIN_ENDSTOP_HIT_STATE HIGH
#define I_MAX_ENDSTOP_HIT_STATE HIGH
#define J_MIN_ENDSTOP_HIT_STATE HIGH
#define J_MAX_ENDSTOP_HIT_STATE HIGH
#define K_MIN_ENDSTOP_HIT_STATE HIGH
#define K_MAX_ENDSTOP_HIT_STATE HIGH
#define U_MIN_ENDSTOP_HIT_STATE HIGH
#define U_MAX_ENDSTOP_HIT_STATE HIGH
#define V_MIN_ENDSTOP_HIT_STATE HIGH
#define V_MAX_ENDSTOP_HIT_STATE HIGH
#define W_MIN_ENDSTOP_HIT_STATE HIGH
#define W_MAX_ENDSTOP_HIT_STATE HIGH
#define Z_MIN_PROBE_ENDSTOP_HIT_STATE HIGH
#define DEFAULT_AXIS_STEPS_PER_UNIT   { 80, 80, 80, 8.88 }
#define DEFAULT_MAX_FEEDRATE          { 300, 300, 300, 25 }
#define DEFAULT_MAX_ACCELERATION      { 3000, 3000, 100, 10000 }
#define DEFAULT_ACCELERATION          3000    // X, Y, Z and E acceleration for printing moves
#define DEFAULT_RETRACT_ACCELERATION  3000    // E acceleration for retracts
#define DEFAULT_TRAVEL_ACCELERATION   3000    // X, Y, Z acceleration for travel (non printing) moves
#define DEFAULT_EJERK    5.0  // May be used by Linear Advance
  #define JUNCTION_DEVIATION_MM 0.013 // (mm) Distance from real junction edge
  #define JD_HANDLE_SMALL_SEGMENTS    // Use curvature estimation instead of just the junction angle
#define Z_MIN_PROBE_USES_Z_MIN_ENDSTOP_PIN
#define NOZZLE_TO_PROBE_OFFSET { 10, 10, 0 }
#define PROBING_TOOL 0
#define PROBING_MARGIN 10
#define XY_PROBE_FEEDRATE (133*60)
#define Z_PROBE_FEEDRATE_FAST (4*60)
#define Z_PROBE_FEEDRATE_SLOW (Z_PROBE_FEEDRATE_FAST / 2)
#define Z_CLEARANCE_DEPLOY_PROBE   10 // Z Clearance for Deploy/Stow
#define Z_CLEARANCE_BETWEEN_PROBES  5 // Z Clearance between probe points
#define Z_CLEARANCE_MULTI_PROBE     5 // Z Clearance between multiple probes
#define Z_PROBE_LOW_POINT          -2 // Farthest distance below the trigger-point to go before stopping
#define Z_PROBE_OFFSET_RANGE_MIN -20
#define Z_PROBE_OFFSET_RANGE_MAX 20
#define X_ENABLE_ON 0
#define Y_ENABLE_ON 0
#define Z_ENABLE_ON 0
#define E_ENABLE_ON 0 // For all extruders
#define I_ENABLE_ON 0
#define DISABLE_OTHER_EXTRUDERS   // Keep only the active extruder enabled
#define INVERT_X_DIR true
#define INVERT_Y_DIR false
#define INVERT_Z_DIR true
#define INVERT_I_DIR false
#define INVERT_E0_DIR false
#define INVERT_E1_DIR false
#define INVERT_E2_DIR false
#define INVERT_E3_DIR false
#define INVERT_E4_DIR false
#define INVERT_E5_DIR false
#define INVERT_E6_DIR false
#define INVERT_E7_DIR false
#define X_HOME_DIR -1
#define Y_HOME_DIR -1
#define Z_HOME_DIR 1
#define I_HOME_DIR -1
#define X_BED_SIZE 850
#define Y_BED_SIZE 450
#define X_MIN_POS 0
#define Y_MIN_POS 0
#define Z_MIN_POS -35
#define X_MAX_POS X_BED_SIZE
#define Y_MAX_POS Y_BED_SIZE
#define Z_MAX_POS 0
#define I_MIN_POS 0
#define I_MAX_POS 359
#define MIN_SOFTWARE_ENDSTOPS
  #define MIN_SOFTWARE_ENDSTOP_X
  #define MIN_SOFTWARE_ENDSTOP_Y
  #define MIN_SOFTWARE_ENDSTOP_Z
  #define MIN_SOFTWARE_ENDSTOP_I
  #define MIN_SOFTWARE_ENDSTOP_J
  #define MIN_SOFTWARE_ENDSTOP_K
  #define MIN_SOFTWARE_ENDSTOP_U
  #define MIN_SOFTWARE_ENDSTOP_V
  #define MIN_SOFTWARE_ENDSTOP_W
#define MAX_SOFTWARE_ENDSTOPS
  #define MAX_SOFTWARE_ENDSTOP_X
  #define MAX_SOFTWARE_ENDSTOP_Y
  #define MAX_SOFTWARE_ENDSTOP_Z
  #define MAX_SOFTWARE_ENDSTOP_I
  #define MAX_SOFTWARE_ENDSTOP_J
  #define MAX_SOFTWARE_ENDSTOP_K
  #define MAX_SOFTWARE_ENDSTOP_U
  #define MAX_SOFTWARE_ENDSTOP_V
  #define MAX_SOFTWARE_ENDSTOP_W
#define MANUAL_Z_HOME_POS 0
#define HOMING_FEEDRATE_MM_M { (50*60), (50*60), (4*60), (4*60) }
#define VALIDATE_HOMING_ENDSTOPS
#define EEPROM_CHITCHAT       // Give feedback on EEPROM commands. Disable to save PROGMEM.
#define EEPROM_BOOT_SILENT    // Keep M503 quiet and only give errors during first load
#define HOST_KEEPALIVE_FEATURE        // Disable this if your host doesn't like keepalive messages
#define DEFAULT_KEEPALIVE_INTERVAL 2  // Number of seconds between "busy" messages. Set with M113.
#define BUSY_WHILE_HEATING            // Some hosts require "busy" messages even during heating
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

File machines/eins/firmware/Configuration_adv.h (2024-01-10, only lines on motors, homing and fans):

#define E0_AUTO_FAN_PIN -1
#define E1_AUTO_FAN_PIN -1
#define E2_AUTO_FAN_PIN -1
#define E3_AUTO_FAN_PIN -1
#define E4_AUTO_FAN_PIN -1
#define E5_AUTO_FAN_PIN -1
#define E6_AUTO_FAN_PIN -1
#define E7_AUTO_FAN_PIN -1
#define CHAMBER_AUTO_FAN_PIN -1
#define COOLER_AUTO_FAN_PIN -1
#define HOMING_BUMP_MM      { 5, 5, 2, 2 }       // (linear=mm, rotational=°) Backoff from endstops after first bump
#define HOMING_BUMP_DIVISOR { 2, 2, 4, 4 }       // Re-Bump Speed Divisor (Divides the Homing Feedrate)
#define MICROSTEP_MODES { 16, 16, 16, 16, 16, 16 } // [1,2,4,8,16]
    #define X_CURRENT       800        // (mA) RMS current. Multiply by 1.414 for peak current.
    #define X_CURRENT_HOME  X_CURRENT  // (mA) RMS current for sensorless homing
    #define X_MICROSTEPS     16        // 0..256
    #define Y_CURRENT       800
    #define Y_CURRENT_HOME  Y_CURRENT
    #define Y_MICROSTEPS     16
    #define Z_CURRENT       800
    #define Z_CURRENT_HOME  Z_CURRENT
    #define Z_MICROSTEPS     16
    #define I_CURRENT      400
    #define I_CURRENT_HOME I_CURRENT
    #define I_MICROSTEPS    16
  #define X_HYBRID_THRESHOLD     100  // [mm/s]
  #define X2_HYBRID_THRESHOLD    100
  #define Y_HYBRID_THRESHOLD     100
  #define Y2_HYBRID_THRESHOLD    100
  #define Z_HYBRID_THRESHOLD       3
  #define Z2_HYBRID_THRESHOLD      3
  #define Z3_HYBRID_THRESHOLD      3
  #define Z4_HYBRID_THRESHOLD      3
  #define I_HYBRID_THRESHOLD       3  // [linear=mm/s, rotational=°/s]
  #define J_HYBRID_THRESHOLD       3  // [linear=mm/s, rotational=°/s]
  #define K_HYBRID_THRESHOLD       3  // [linear=mm/s, rotational=°/s]
  #define U_HYBRID_THRESHOLD       3  // [mm/s]
  #define V_HYBRID_THRESHOLD       3
  #define W_HYBRID_THRESHOLD       3
  #define E0_HYBRID_THRESHOLD     30
  #define E1_HYBRID_THRESHOLD     30
  #define E2_HYBRID_THRESHOLD     30
  #define E3_HYBRID_THRESHOLD     30
  #define E4_HYBRID_THRESHOLD     30
  #define E5_HYBRID_THRESHOLD     30
  #define E6_HYBRID_THRESHOLD     30
  #define E7_HYBRID_THRESHOLD     30

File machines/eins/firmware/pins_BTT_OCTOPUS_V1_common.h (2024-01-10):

/**
 * Marlin 3D Printer Firmware
 * Copyright (c) 2021 MarlinFirmware [https://github.com/MarlinFirmware/Marlin]
 *
 * Based on Sprinter and grbl.
 * Copyright (c) 2011 Camiel Gubbels / Erik van der Zalm
 *
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
 */
#pragma once

#include "env_validate.h"

#define HAS_OTG_USB_HOST_SUPPORT                  // USB Flash Drive support

// Machdyne PNP uses physical limit switches:
//#define USES_DIAG_JUMPERS

// Onboard I2C EEPROM
#if ANY(NO_EEPROM_SELECTED, I2C_EEPROM)
  #undef NO_EEPROM_SELECTED
  #define I2C_EEPROM
  #define MARLIN_EEPROM_SIZE              0x1000  // 4K (AT24C32)
  #define SOFT_I2C_EEPROM                         // Force the use of Software I2C
  #define I2C_SCL_PIN                       PB8
  #define I2C_SDA_PIN                       PB9
#endif

// Avoid conflict with TIMER_TONE
#define STEP_TIMER 8

//
// Servos
//
#define SERVO0_PIN                          PB6

// Machdyne PNP limit switches

#define X_STOP_PIN								PG6
#define Y_STOP_PIN								PG9
#define Z_STOP_PIN								PG10

//#define X_MIN_PIN									PG6
//#define Y_MIN_PIN									PG9
//#define Z_MIN_PIN									PG10

#define I_STOP_PIN									PG12
//#define Y_MAX_PIN									PG13
//#define Z_MAX_PIN									PG14

/*

//
// Trinamic Stallguard pins
//
#define X_DIAG_PIN                          PG6   // X-STOP
#define Y_DIAG_PIN                          PG9   // Y-STOP
#define Z_DIAG_PIN                          PG10  // Z-STOP
#define Z2_DIAG_PIN                         PG11  // Z2-STOP
#define E0_DIAG_PIN                         PG12  // E0DET
#define E1_DIAG_PIN                         PG13  // E1DET
#define E2_DIAG_PIN                         PG14  // E2DET
#define E3_DIAG_PIN                         PG15  // E3DET

//
// Limit Switches
//
#ifdef X_STALL_SENSITIVITY
  #define X_STOP_PIN                  X_DIAG_PIN
  #if X_HOME_TO_MIN
    #define X_MAX_PIN                E0_DIAG_PIN  // E0DET
  #else
    #define X_MIN_PIN                E0_DIAG_PIN  // E0DET
  #endif
#elif NEEDS_X_MINMAX
  #ifndef X_MIN_PIN
    #define X_MIN_PIN                 X_DIAG_PIN  // X-STOP
  #endif
  #ifndef X_MAX_PIN
    #define X_MAX_PIN                E0_DIAG_PIN  // E0DET
  #endif
#else
  #define X_STOP_PIN                  X_DIAG_PIN  // X-STOP
#endif

#ifdef Y_STALL_SENSITIVITY
  #define Y_STOP_PIN                  Y_DIAG_PIN
  #if Y_HOME_TO_MIN
    #define Y_MAX_PIN                E1_DIAG_PIN  // E1DET
  #else
    #define Y_MIN_PIN                E1_DIAG_PIN  // E1DET
  #endif
#elif NEEDS_Y_MINMAX
  #ifndef Y_MIN_PIN
    #define Y_MIN_PIN                 Y_DIAG_PIN  // Y-STOP
  #endif
  #ifndef Y_MAX_PIN
    #define Y_MAX_PIN                E1_DIAG_PIN  // E1DET
  #endif
#else
  #define Y_STOP_PIN                  Y_DIAG_PIN  // Y-STOP
#endif

#ifdef Z_STALL_SENSITIVITY
  #define Z_STOP_PIN                  Z_DIAG_PIN
  #if Z_HOME_TO_MIN
    #define Z_MAX_PIN                E2_DIAG_PIN  // PWRDET
  #else
    #define Z_MIN_PIN                E2_DIAG_PIN  // PWRDET
  #endif
#elif NEEDS_Z_MINMAX
  #ifndef Z_MIN_PIN
    #define Z_MIN_PIN                 Z_DIAG_PIN  // Z-STOP
  #endif
  #ifndef Z_MAX_PIN
    #define Z_MAX_PIN                E2_DIAG_PIN  // PWRDET
  #endif
#else
  #define Z_STOP_PIN                  Z_DIAG_PIN  // Z-STOP
#endif

*/

//
// Z Probe (when not Z_MIN_PIN)
//
#ifndef Z_MIN_PROBE_PIN
  #define Z_MIN_PROBE_PIN                   PB7
#endif

//
// Filament Runout Sensor
//
#define FIL_RUNOUT_PIN                      PG12  // E0DET
#define FIL_RUNOUT2_PIN                     PG13  // E1DET
#define FIL_RUNOUT3_PIN                     PG14  // E2DET
#define FIL_RUNOUT4_PIN                     PG15  // E3DET

//
// Power Supply Control
//
#ifndef PS_ON_PIN
  #define PS_ON_PIN                         PE11  // PS-ON
#endif

//
// Power Loss Detection
//
#ifndef POWER_LOSS_PIN
  #define POWER_LOSS_PIN                    PC0   // PWRDET
#endif

//
// Misc. Functions
//
#define LED_PIN                             PA13

//
// Steppers
//
#define X_STEP_PIN                          PF13  // MOTOR 0
#define X_DIR_PIN                           PF12
#define X_ENABLE_PIN                        PF14
#ifndef X_CS_PIN
  #define X_CS_PIN                          PC4
#endif

// NOTE: X and Y have been swapped for Machdyne PNP:

#define Z_STEP_PIN                          PG0   // MOTOR 1
#define Z_DIR_PIN                           PG1
#define Z_ENABLE_PIN                        PF15
#ifndef Z_CS_PIN
  #define Z_CS_PIN                          PD11
#endif

#define Y_STEP_PIN                          PF11  // MOTOR 2
#define Y_DIR_PIN                           PG3
#define Y_ENABLE_PIN                        PG5
#ifndef Y_CS_PIN
  #define Y_CS_PIN                          PC6
#endif

#define I_STEP_PIN                         PG4   // MOTOR 3
#define I_DIR_PIN                          PC1
#define I_ENABLE_PIN                       PA0
#ifndef I_CS_PIN
  #define I_CS_PIN                         PC7
#endif
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

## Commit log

2024-06-18 add assembly docs
    [dc.scad, gmbc.scad]
2024-09-20 raise z axis rails by 5mm
    [zgm.scad]

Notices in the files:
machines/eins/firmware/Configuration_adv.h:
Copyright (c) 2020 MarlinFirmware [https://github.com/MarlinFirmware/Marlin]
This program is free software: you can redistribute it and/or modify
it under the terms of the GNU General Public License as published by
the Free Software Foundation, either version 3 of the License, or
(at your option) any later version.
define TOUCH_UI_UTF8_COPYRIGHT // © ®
